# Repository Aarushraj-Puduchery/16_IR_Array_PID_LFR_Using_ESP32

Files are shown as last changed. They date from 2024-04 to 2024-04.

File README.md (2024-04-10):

# 16_IR_Array_PID_LFR_Using_ESP32

This is my Second Attempt to make a Line Follower Bot, I tried to correct the mistakes I made in my first LFR and here we go This is my new 16 IR Sensor Line Follower Bot using ESP32.

Why ESP32 because it has a High Clock Speed.

A line follower bot is a type of autonomous robotic vehicle designed to follow a predefined path or track marked with contrasting lines, typically black on a light-coloured surface or vice versa. These robots employ a combination of sensors, such as infrared or optical sensors, to detect the contrast between the line and the surrounding area. By continuously analyzing the sensor data, the bot makes real-time decisions on how to adjust its wheels or propulsion system to stay centred on the line.

Line follower bots are popular in robotics competitions and educational settings, as they provide an engaging way to introduce students and enthusiasts to basic robotics principles, sensor technology, and programming. They serve as a fundamental example of closed-loop control systems and can be customized with various features, like obstacle avoidance and speed adjustments, to make them more versatile and adaptable to different scenarios. Line follower bots can be a great starting point for those interested in exploring the world of robotics and automation.

A PID Line Follower Bot using an ESP32 Microcontroller is a small autonomous robot that uses infrared sensors to follow a designated path. It employs a PID (Proportional-Integral-Derivative) control algorithm to continuously adjust its motor speeds based on sensor feedback, maintaining alignment with the path. The ESP32 microcontroller processes the sensor data and sends control signals to the motors, allowing the bot to track lines, it is a popular choice for educational robotics projects and competitions.

## LFR Images

|Top View|Bottom View|
|---|---|
|Left view|Right View|

## Schematic Diagram

Schematic_New-16-ir-array-PID-LFR

## Chassis Design

|Components Placement|LFR Chassic|
|---|---|

## Wheels Design

|||
|---|---|
|||

>[!NOTE]
>Wheels Design Files are Uploaded and Can be 3D Printed Directly.

## Menu Graphic

|Start|Settings|Kp|
|---|---|---|
|Kd|Calibrate|Sensor Values|
|Run|

## Dry Run Video

https://github.com/Aarushraj-Puduchery/16_IR_Array_PID_LFR_Using_ESP32/assets/97360295/b0accbfe-f4fa-431e-92e3-81439fa5fb1b

## Components List
|S.No|  Name  | Cost | Quantity | Total Cost | Link |
|---| --- | --- | --- | --- | --- |
|1| ESP32 38 pin Development Board | ₹463.00 | 1 | ₹463.00 | https://robu.in/product/esp32-38pin-development-board-wifibluetooth-ultra-low-power-consumption-dual-core/ |
|2| TCRT5000 - Reflective Infrared Optical Sensor | ₹14.00 | 16 | ₹84.00 | https://www.electronicscomp.com/tcrt-5000-reflective-infrared-optical-sensor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 |
|3| CD74HC4067 16 Channel Multiplexer | ₹47.00 | 1 | ₹47.00 | https://www.electronicscomp.com/cd74hc4067-16-channel-multiplexer-breakout-board-module-india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 |
|4| N20-12V-1000 Rpm Micro Metal Gear Motor DC Encoder | ₹448.00 | 2 | ₹1792.00 | https://robokits.co.in/motors/n20-metal-gear-micro-motors/n20-metal-gear-encoder-motor/ga12-n20-12v-1000-rpm-all-metal-gear-micro-dc-encoder-motor-with-precious-meta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 |
|5| TB6612FNG Dual Channel Motor Driver | ₹349.00 | 1 | ₹349.00 | https://www.robojunkies.com/products/tb6612fng-dual-channel-motor-driver-breakout |
|6| Mounting Bracket for N20 Micro Gear motors | ₹29.00 | 2 | ₹58.00 | https://robu.in/product/mounting-bracket-n20-micro-gear-motors/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 |
|7| Mini MP1584 DC-DC 3A Adjustable Buck module | ₹48.00 | 1 | ₹48.00 | https://robu.in/product/mini-mp1584-dc-dc-adjustable-buck-module-3a/ |
|8| N20 mini-vacuum steel-ball caster wheel | ₹75.00 | 1 | ₹75.00 | https://robu.in/product/ball-castors/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 |
|9| Orange 850mah 3S 30C/60C (11.1V) Lithium Polymer Battery Pack | ₹999.00 | 1 | ₹999.00 | https://robu.in/product/orange-850mah-3s-30c-60c-lithium-polymer-battery-pack-lipo/ |
|10| Nylon XT60 Connectors Male/Female (1 pairs) | ₹69.00 | 1 | ₹69.00 | https://robu.in/product/amass-nylon-xt60-connectors-male-female-pair/ |
|11| Cricket Bat Grip | ₹100.00 | 1 | ₹100.00 | Local Shop |
|12| 1.3 inch 128×64 White OLED Display | ₹359.00 | 1 | ₹359.00 | https://robu.in/product/1-3-inch-i2c-iic-oled-lcd-module-4pin-with-vcc-gnd-white/ |
|13| 5 x 7 cm Universal PCB Prototype Board Single-Sided 2.54mm Hole Pitch | ₹33.00 | 2 | ₹66.00 | https://robu.in/product/5-x-7-cm-universal-pcb-prototype-board-single-sided-2-54mm-hole-pitch/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 | 
|14| 3 Pin SPDT Toggle switch | ₹70.00 | 1 | ₹70.00 | https://robu.in/product/5a-3-pin-spdt-toggle-switch/ |
|15| Tactile Push Button | ₹5.00 | 6 | ₹30.00 | https://robu.in/product/12x12x7-3mm-tactile-push-button-switch-round/ |
|16| Female Header pins | ₹20.00 | 5 | ₹100.00 | https://robu.in/product/2-54mm-1x40-pin-female-single-row-header-strip-pack-of-10/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 |
|17| Laser Cutting For Chassis | ₹205.00 | 1 | ₹205.00 | https://robu.in/product/online-laser-cutting-service/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 |
|18| 4mm SPDT 1P2T Slide Switch | ₹5.00 | 2 | ₹10.00 | https://robu.in/product/4mm-spdt-1p2t-slide-switch-pack-of-10/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 |
|19| 10k resistor 1/4W | ₹0.50 | 22 | ₹11.00 | https://robu.in/product/10k-ohm-0-25w-metal-film-resistor-pack-of-100/ |
|20| 220 resistor 1/4W | ₹0.50 | 16 | ₹8.00 | https://robu.in/product/220-ohm-resistor-0-25w-metal-film-pack-of-100/ |

> [!NOTE]
> Components price may vary.

## Source Code
1. `main.py` file which contains the basic setup and Run.
2. `bitmap.py` file contains all the menu graphics.
3. `KpValue.csv` and `KdValue.csv` are the files which store the kp and kd values.
4. `ssd1106.py` file is the library used for Oled display.
5. `framebuf.py` file is the library used for displaying graphics on Oled display.

>[!IMPORTANT]
>All the Files must be saved on the ESP32 Memory.

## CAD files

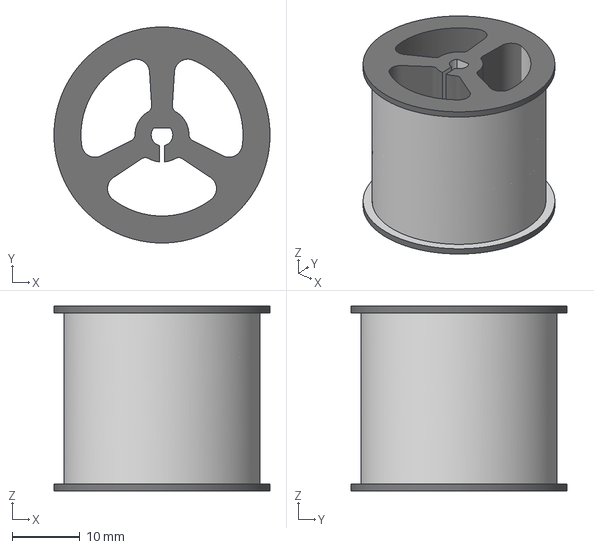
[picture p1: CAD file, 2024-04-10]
3D Printed Wheels Files/N20 Motor Wheel(2.7cm)_19 March v1.3mf
32.0 x 32.0 x 27.4 mm

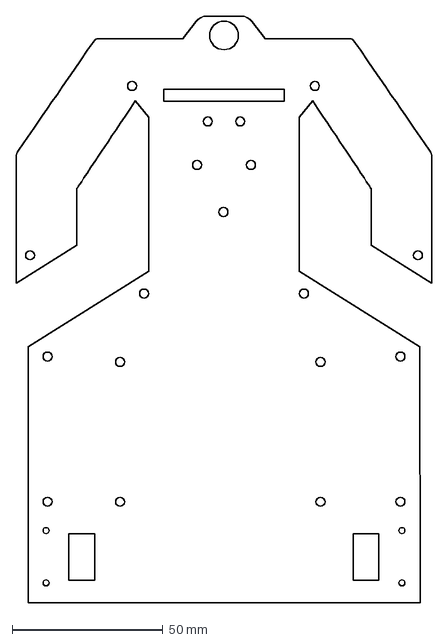
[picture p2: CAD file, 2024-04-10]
LFR Chassic Design/LFR Chassic.dxf
137.8 x 194.6 mm

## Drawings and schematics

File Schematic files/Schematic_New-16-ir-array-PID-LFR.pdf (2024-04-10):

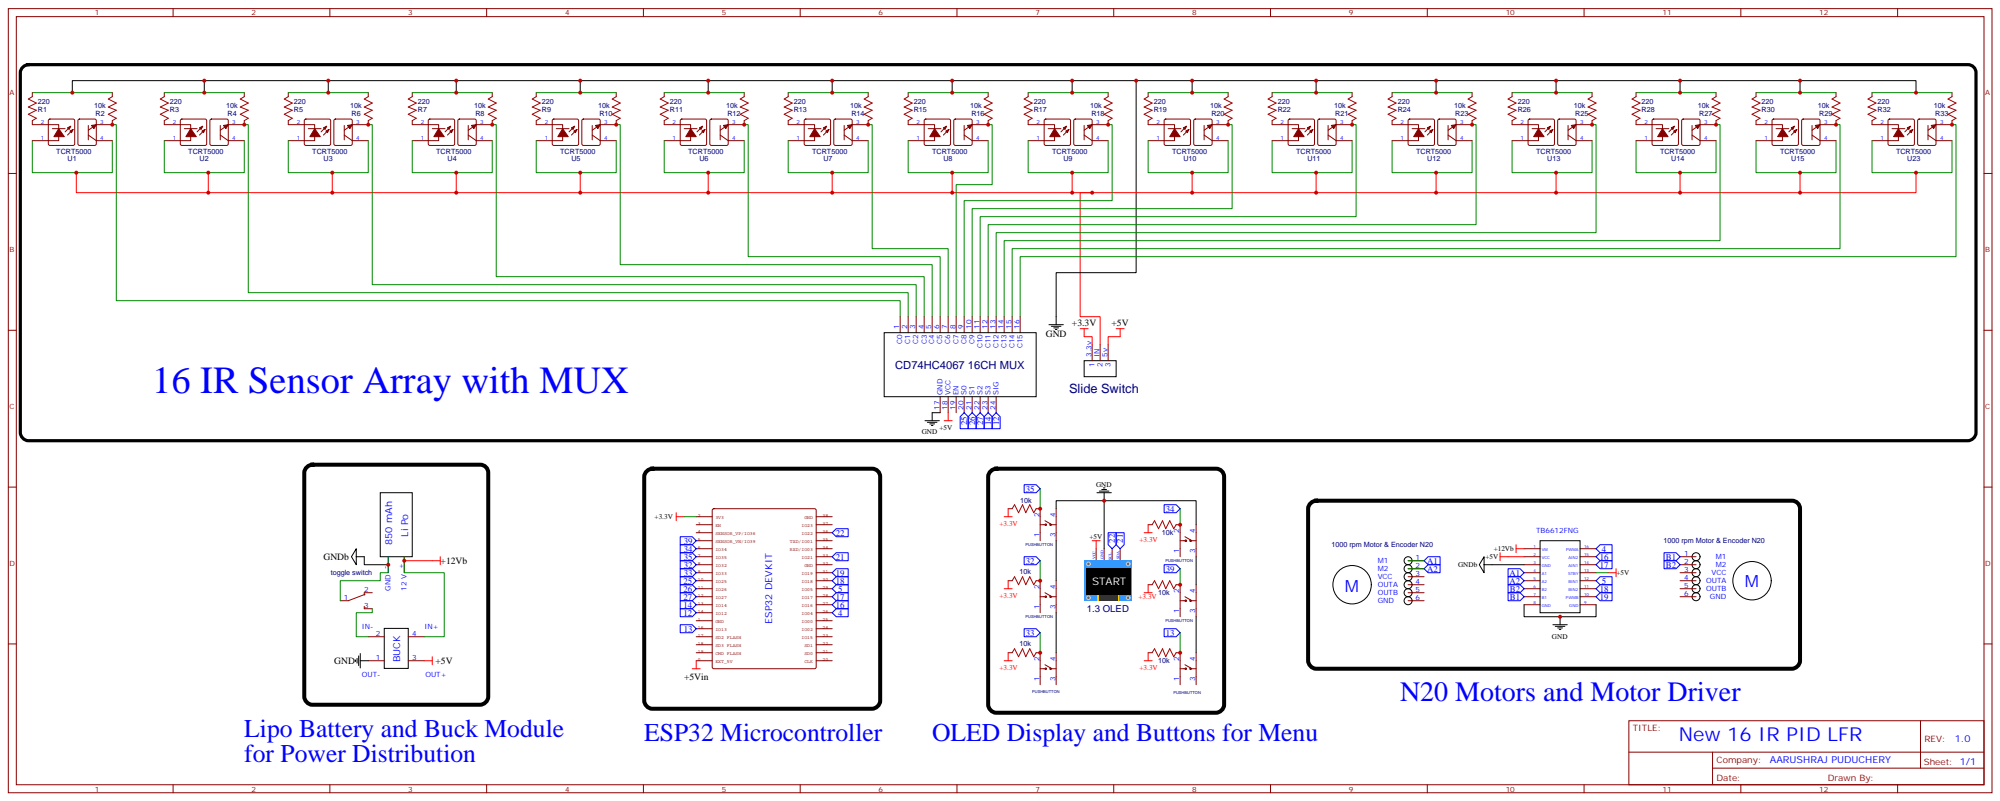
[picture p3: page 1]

16 IR Sensor Array with MUX

N20 Motors and Motor Driver

Lipo Battery and Buck Module
for Power Distribution

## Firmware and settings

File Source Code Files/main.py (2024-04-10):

#Simple Line Following Code using PID

from machine import Pin,PWM,I2C,ADC
from utime import sleep,sleep_ms,ticks_ms
import machine
import sh1106
import framebuf
import bitmap
machine.freq(240000000)

# Define pin numbers connected to buttons
UP = 35  # Up Button
DP = 34  # Down B
LP = 32  # Left B
RP = 39  # Right Button
SP = 33  # Select Button
BP = 13  # Back Button

UB = Pin(UP,Pin.IN)
DB = Pin(DP,Pin.IN)
LB = Pin(LP,Pin.IN)
RB = Pin(RP,Pin.IN)
SB = Pin(SP,Pin.IN)
BB = Pin(BP,Pin.IN)

count1,count2,count3 = 0,0,0
pr1 = 0
pr2,pr3 = 0,0
detime = 0
detime2 = 0
UBv,DBv,LBv,RBv,SBv,BBv = 0,0,0,0,0,0

def callback(pin):
    global count1,count2,count3,pr1,pr2,pr3,detime,detime2,UBv,DBv,LBv,RBv,SBv,BBv
    if str(pin) == "Pin(35)" and (ticks_ms() - detime > 300):
        count1 = count1 + 1
        UBv = 1
        print("UB")
        detime = ticks_ms()
    
    elif str(pin) == "Pin(34)" and (ticks_ms() - detime > 300):
        count1 = count1 - 1
        DBv = 1
        print("DB")
        detime = ticks_ms()

    elif str(pin) == "Pin(32)" and (ticks_ms() - detime > 300):
        count2 = count2 + 1
        LBv = 1
        print("LB")
        detime = ticks_ms()
        
    elif str(pin) == "Pin(39)" and (ticks_ms() - detime > 300):
        count2 = count2 - 1
        RBv = 1
        print("RB")
        detime = ticks_ms()
        
    elif str(pin) == "Pin(33)" and (ticks_ms() - detime2 > 300):
        count3 = count3 + 1
        SBv = 1
        print("SB")
        detime2 = ticks_ms()
        
    elif str(pin) == "Pin(13)" and (ticks_ms() - detime > 300):
        count3 = count3 - 1
        BBv = 1
        print("BB")
        detime = ticks_ms()


UB.irq(trigger=Pin.IRQ_FALLING, handler=callback)
DB.irq(trigger=Pin.IRQ_FALLING, handler=callback)
LB.irq(trigger=Pin.IRQ_FALLING, handler=callback)
RB.irq(trigger=Pin.IRQ_FALLING, handler=callback)
SB.irq(trigger=Pin.IRQ_FALLING, handler=callback)
BB.irq(trigger=Pin.IRQ_FALLING, handler=callback)

#Oled Display
sda=Pin(21)
scl=Pin(22)
i2c = I2C(0, scl=scl, sda=sda, freq=400000)
oled = sh1106.SH1106_I2C(128, 64, i2c, Pin(4), 0x3c)
oled.sleep(False)



#Motors
MAF = Pin(17,Pin.OUT)
MAR = Pin(16,Pin.OUT)
MBF = Pin(5,Pin.OUT)
MBR = Pin(18,Pin.OUT)
MAC = PWM(Pin(4))
MBC = PWM(Pin(19))

MAC.freq(1000)
MBC.freq(1000)

# Define pins for multiplexer control
sensor_value = [0,0,0,0,0,0,0,0,0,0,0,0,0,0,0,0]
s0 = Pin(25, Pin.OUT)
s1 = Pin(26, Pin.OUT)
s2 = Pin(27, Pin.OUT)
s3 = Pin(14, Pin.OUT)

# Define analog input pin
analog_pin = Pin(12)


maxvalue = [0,0,0,0,0,0,0,0,0,0,0,0,0,0,0,0]
minvalue = [0,0,0,0,0,0,0,0,0,0,0,0,0,0,0,0]
threshold = [0,0,0,0,0,0,0,0,0,0,0,0,0,0,0,0]
sensor_val = [0,0,0,0,0,0,0,0,0,0,0,0,0,0,0,0]
sensor_arr = [0,0,0,0,0,0,0,0,0,0,0,0,0,0,0,0]
ir_val = [0,0,0,0,0,0,0,0,0,0,0,0,0,0,0,0]
mode = -1

isBlackLine = 1
P, D, I, PIDvalue = 0,0,0,0
PreviousError = 0
error = 0.0
sensorWeight = [ 9, 7, 5, 4, 3, 2, 1, 0, 0, -1, -2, -3, -4, -5, -7, -9 ]
lfSpeed = 36000
currentSpeed = 35000
activeSensors = 0
op = 0

KpFile = open("kpfile.csv","r")
Kp = float(KpFile.read())
KdFile = open("kdfile.csv","r")
Kd = float(KdFile.read())
KpFile.close()
KdFile.close()
Ki = 0

def read_ir_sensor(channel):
    s0.value(channel & 0x01)
    s1.value((channel >> 1) & 0x01)
    s2.value((channel >> 2) & 0x01)
    s3.value((channel >> 3) & 0x01)
    sleep_ms(1)  # Wait for the channel to settle
    adc = ADC(analog_pin)
    adc.atten(ADC.ATTN_11DB)
    return adc.read()

def motor1run(motorSpeed):
    if (motorSpeed > 0):
        MAF.value(1)
        MAR.value(0)
        MAC.duty_u16(int(motorSpeed))
    elif(motorSpeed < 0):
        MAF.value(0)
        MAR.value(1)
        MAC.duty_u16(abs(int(motorSpeed)))
    else:
        MAF.value(1)
        MAR.value(1)
        MAC.duty_u16(0)

def motor2run(motorSpeed):
    if (motorSpeed > 0):
        MBF.value(1)
        MBR.value(0)
        MBC.duty_u16(int(motorSpeed))
    elif(motorSpeed < 0):
        MBF.value(0)
        MBR.value(1)
        MBC.duty_u16(abs(int(motorSpeed)))
    else:
        MBF.value(1)
        MBR.value(1)
        MBC.duty_u16(0)

def calibrate():
    motor1run(0)
    motor2run(0)
    fbuf = framebuf.FrameBuffer(bitmap.calibrate_text, 128, 64, framebuf.MONO_HLSB)
    oled.fill(0)
    oled.blit(fbuf, 0, 0, 0)          
    oled.show()
    #step 1: fill the min and max list with current values
    for i in range(16):
        minvalue[i] = read_ir_sensor(i)
        maxvalue[i] = read_ir_sensor(i)

    #step 2: sort the max and min values of all sensors by moving the bot left and right
    for j in range(80):
        motor1run(27000)
        motor2run(-27000)
        for i in range(16):
            if(read_ir_sensor(i) < minvalue[i]):
                minvalue[i] = read_ir_sensor(i)
            if(read_ir_sensor(i) > maxvalue[i]):
                maxvalue[i] = read_ir_sensor(i)

    #step 3: calculate the threshold values
    print("threshold")
    for i in range(16):
        threshold[i] = (minvalue[i] + maxvalue[i])/2
        print(threshold[i],end=" ")
    motor1run(0)
    motor2run(0)

def convert(x, in_min, in_max, out_min, out_max):
    return (x - in_min) * (out_max - out_min) // (in_max - in_min) + out_min
    
def readline():
    global onLine,isBlackLine,minvalue,maxvalue
    onLine = 0
    for i in range(16):
        if(isBlackLine):
            sensor_val[i] = convert(read_ir_sensor(i), minvalue[i], maxvalue[i], 0, 1000)
        else:
            sensor_val[i] = convert(read_ir_sensor(i), minvalue[i], maxvalue[i], 1000, 0)
        
        sensor_val[i] = min(max(sensor_val[i], 0), 1000)
        sensor_arr[i] = sensor_val[i] < 450
        if(sensor_arr[i]):
            onLine = 1
            
        if(isBlackLine == 1 and sensor_arr[i]):
            onLine = 1
        if(isBlackLine == 0 and not(sensor_arr[i])):
            onLine = 1

def linefollow():
    global error,activeSensors,P,I,D,PIDvalue,PreviousError,lsp,Kp,Ki,Kd,rsp
    error=0
    activeSensors = 0
    for i in range(16):
        error = error + (sensorWeight[i] * sensor_arr[i] * (1000 - sensor_val[i]))
        activeSensors += sensor_arr[i]
    
    error = error/activeSensors
    
    P = error
    I = I + error
    D = error - PreviousError
    
    PIDvalue = (Kp * P) + (Ki * I) + (Kd * D)
    PreviousError = error
    
    lsp = currentSpeed - PIDvalue
    rsp = currentSpeed + PIDvalue
    
    fbuf = framebuf.FrameBuffer(bitmap.letgo_text, 128, 64, framebuf.MONO_HLSB)
    oled.fill(0)
    oled.blit(fbuf, 0, 0, 0)
    oled.text("lsp = ",0,40)
    oled.text("rsp = ",0,50)
    oled.text(str(lsp),45,40)
    oled.text(str(rsp),45,50)
    oled.show()
    
    if(lsp > 65535):
        lsp = 65535
    if(lsp < 0):
        lsp = 0
    if(rsp > 65535):
        rsp = 65535
    if(rsp < 0):
        rsp = 0
    motor1run(lsp);
    motor2run(rsp);
    
def ir_show():
    global ir_val
    for i in range(1,17):
        if (i <= 8):
            oled.text(str(i),((8*(i-1))-1),55)
        else:
            oled.text(str(17 - i),(8*(i-1)-1),55)
        oled.show()
    while True:
        oled.fill_rect(0,0,128,45,0)
        for i in range(16):
            ir_val[i] = convert(read_ir_sensor(i), minvalue[i], maxvalue[i], 1, 45)
            ir_val[i] = min(max(ir_val[i],1),45)
        for i in range(16):
            oled.fill_rect((i)*8,0,6,45,1)
            oled.fill_rect((i)*8,0,6,45 - ir_val[i],0)
        oled.show()
        if SBv == 1:
            break

    
def setup_val():
    global count1,count2,count3,Kp,Kd,UBv,DBv,LBv,RBv,SBv,BBv,mode,op
    menu = [bitmap.start_menu, bitmap.setting_menu]
    fbuf = framebuf.FrameBuffer(menu[count1], 128, 64, framebuf.MONO_HLSB)
    oled.blit(fbuf, 0, 0, 0)          
    oled.show()
    oled.fill(0)
    if BBv == 1:
        fbuf = framebuf.FrameBuffer(menu[count1], 128, 64, framebuf.MONO_HLSB)
        oled.blit(fbuf, 0, 0, 0)    
        oled.show()
        BBv = 0
        
    if (UBv == 1) or (DBv == 1):
        count1 = (count1) % len(menu)
        oled.fill(0)
        fbuf = framebuf.FrameBuffer(menu[count1], 128, 64, framebuf.MONO_HLSB)
        oled.blit(fbuf, 0, 0, 0)
        oled.show()
        UBv, DBv = 0,0
    if count1 == 0 and SBv == 1:
        mode = 1
    if count1 == 1 and SBv == 1:
        count1 = 0
        SBv = 0
        oled.fill(0)
        oled.show()
        while True:
            setting = [bitmap.Kp_menu,bitmap.Kd_menu]
            settingfile = ["kp","kd"]
            fbuf = framebuf.FrameBuffer(setting[count1], 128, 64, framebuf.MONO_HLSB)
            oled.fill(0)
            oled.blit(fbuf, 0, 0, 0)          
            oled.show()
            if (UBv == 1) or (DBv == 1):
                count1 = (count1) % len(setting)
                fbuf = framebuf.FrameBuffer(setting[count1], 128, 64, framebuf.MONO_HLSB)
                oled.fill(0)
                oled.blit(fbuf, 0, 0, 0)          
                oled.show()
                UBv, DBv = 0,0
                op = count1
            
            if SBv == 1:
                count1 = 0
                oled.fill(0)
                BBv = 0
                while True:
                    SBv = 0
                    if UBv == 1 or DBv == 1:
                        count1 = max(-3,min(count1,4))
                        UBv, DBv = 0,0
                        oled.fill(0)
                    oled.text(str(10**(-1*count1)),55,40)
                    oled.show()
                    KpFile = open(settingfile[op]+"file.csv","r")
                    Kp = float(KpFile.read())
                    KpText = str(Kp)
                    oled.text(KpText, 35, 18)
                    oled.show()
                    KpFile.close()
                    if LBv == 1:
                        Kp = (Kp - (1*pow(10,-1*count1)))
                        KpFile = open(settingfile[op]+"file.csv","r+")
                        KpFile.seek(0)
                        KpText = str(Kp)
                        KpFile.write(KpText)
                        KpFile.close()
                        oled.text(KpText, 35, 18)
                        oled.show()
                        oled.fill(0)
                        LBv = 0
                    if RBv == 1:
                        Kp = (Kp + (1*pow(10,-1*count1)))
                        KpFile = open(settingfile[op]+"file.csv","r+")
                        KpFile.seek(0)
                        KpText = str(Kp)
                        KpFile.write(KpText)
                        KpFile.close()
                        oled.text(KpText, 35, 18)
                        oled.show()
                        oled.fill(0)
                        RBv = 0
                    if BBv == 1:
                        oled.fill(0)
                        oled.text(settingfile[count1], 0, 0)
                        oled.show()
                        BBv = 0
                        break      
            if BBv == 1:
                BBv = 0
                break
       

while True:
    setup_val()
    if mode == 1:
        mode = 0
        break

oled.fill(0)
KpFile = open("kpfile.csv","r")
KpT = float(KpFile.read())
KpText = str(KpT)
KdFile = open("kdfile.csv","r")
KdT = float(KdFile.read())
KdText = str(KdT)
oled.text("Kp", 50, 0)
oled.text((KpText), 22, 20)
oled.text("Kd", 50, 35)
oled.text((KdText), 22, 55)
oled.show()
KpFile.close()
KdFile.close()
SBv = 0
while SBv == 0:
    pass
calibrate()
SBv = 0
BBv = 0
while SBv == 0:
    ir_show()
    motor1run(0)
    motor2run(0)

SBv = 0
fbuf = framebuf.FrameBuffer(bitmap.letgo_text, 128, 64, framebuf.MONO_HLSB)
oled.fill(0)
oled.blit(fbuf, 0, 0, 0)          
oled.show()
while True:
    readline()
#     if (currentSpeed < lfSpeed):
#         currentSpeed = currentSpeed + 4
    if (onLine == 1):
        linefollow()
    else:
        if error > 0:
            motor1run(-40000)
            motor2run(lsp)
        else:
            motor1run(rsp)
            motor2run(-40000)

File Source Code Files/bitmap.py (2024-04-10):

start_menu = bytearray(b"\x00\x00\x00\x00\x00\x00\x00\x00\x00\x00\x00\x00\x00\x00\x00\x00\x00\x00\x00\x00\x00\x00\x60\x00\x00\x03\x00\x00\x00\x00\x00\x00\x00\x00\x00\x00\x00\x00\xe0\x00\x00\x03\x80\x00\x00\x00\x00\x00\x00\x00\x00\x00\x00\x01\x30\x00\x00\x06\x40\x00\x00\x00\x00\x00\x00\x00\x00\x00\x00\x02\x30\x00\x00\x06\x30\x00\x00\x00\x00\x00\x00\x00\x00\x00\x00\x0c\x18\x00\x00\x0e\x18\x00\x00\x00\x00\x00\x00\x00\x00\x00\x00\x3c\x18\x00\x00\x0c\x1e\x00\x00\x00\x00\x00\x00\x00\x00\x00\x01\xfc\x3c\x00\x00\x1e\x1f\xc0\x00\x00\x00\x00\x00\x00\x00\x00\x1e\x7e\xfe\x00\x00\x1f\xbf\x3c\x00\x00\x00\x00\x00\x00\x00\x00\xf0\x3e\xfe\x00\x00\x3f\xde\x03\x80\x00\x00\x00\x00\x00\x00\x07\xf0\x38\xfe\x00\x00\x3f\x8e\x03\xe0\x00\x00\x00\x00\x00\x00\x39\xf0\x00\x73\x00\x00\x67\x80\x07\xce\x00\x00\x00\x00\x00\x00\x20\xf0\x60\x63\x00\x00\x61\x03\x07\xc2\x00\x00\x00\x00\x00\x01\xc0\xf3\xf0\x01\x80\x00\xe0\x03\xe7\x81\x80\x00\x00\x00\x00\x03\xc0\x83\xf0\xc1\x80\x00\xc1\xc7\xe0\x81\xe0\x00\x00\x00\x00\x07\xe1\x83\xf3\xc3\xc0\x01\xe1\xf7\xe0\xc3\xf0\x00\x00\x00\x00\x07\xf7\x81\xe3\xe7\xc0\x01\xf3\xf3\xc0\xf3\xf0\x00\x00\x00\x00\x03\xff\xc0\x03\xff\xe0\x03\xff\xf0\x00\xf9\xe0\x00\x00\x00\x00\x03\x8f\xc6\x03\xcf\xe0\x03\xf9\xe0\x38\xf8\xe0\x00\x00\x00\x00\x01\x87\x9f\x01\x8e\x30\x07\x38\x40\x7c\xf0\x40\x00\x00\x00\x00\x01\x86\x1f\x80\x04\x38\x06\x10\x00\xfc\x20\x40\x00\x00\x00\x00\x00\x84\x0c\x0f\x04\x18\x0e\x10\x38\x18\x00\xc0\x00\x00\x00\x00\x00\xcc\x00\x3f\x0c\x38\x0e\x18\x7e\x00\x1c\x00\x00\x00\x00\x00\x00\x5c\x00\x1f\x1c\x7c\x0c\x1e\x7c\x04\x1e\x00\x00\x00\x00\x00\x00\x7e\x78\x1c\x3f\x8c\x18\xfe\x0c\x0f\x9f\x00\x00\x00\x00\x00\x00\x3e\xfc\x10\x3f\x86\x30\x7e\x00\x0f\xdf\x00\x00\x00\x00\x00\x00\x38\xf8\xf0\x3e\x06\x30\x1e\x07\xcf\x86\x00\x00\x00\x00\x00\x00\x10\x71\xf1\xf8\x06\x70\x07\xc7\xe7\x80\x00\x00\x00\x00\x00\x00\x00\x01\xff\x80\x02\x60\x00\x7f\xc0\x00\x00\x00\x00\x00\x00\x00\x00\x01\xf8\x00\x00\x60\x00\x0f\xc0\x00\x00\x00\x00\x00\x00\x00\x01\xc7\x80\x00\x00\xc0\x00\x00\x71\xc8\x00\x00\x00\x00\x00\x00\x0f\xec\x00\x00\x00\xc0\x00\x00\x19\xf8\x00\x00\x00\x00\x00\x00\x07\xf0\x00\x00\x01\x80\x00\x00\x07\xf0\x00\x00\x00\x00\x00\x00\x07\xc0\x00\x00\x01\x80\x00\x00\x01\xe0\x00\x00\x00\x00\x00\x00\x03\x80\x00\x00\x03\x20\x00\x00\x00\xe0\x00\x00\x00\x00\x00\x00\x03\x00\x00\x00\x03\x70\x00\x00\x00\x60\x00\x00\x00\x00\x00\x00\x00\x00\x00\x00\x06\x70\x00\x00\x00\x00\x00\x00\x00\x00\x00\x00\x00\x00\x00\x00\x06\x30\x00\x00\x00\x00\x00\x00\x00\x00\x00\x00\x00\x00\x00\x00\x00\x00\x00\x00\x00\x00\x00\x00\x00\x00\x00\x00\x00\x00\x00\x00\x00\x00\x00\x00\x00\x00\x00\x00\x00\x00\x00\x00\x00\x00\x00\x00\x00\x00\x00\x00\x00\x00\x00\x00\x00\x00\x00\x00\x3d\xc0\x00\x0c\x00\x00\x00\x00\x00\x01\x00\x00\x00\x00\x00\x00\x60\x30\xef\xf4\x03\x80\x08\xe0\x3d\xfc\x80\x00\x00\x00\x00\x00\x83\xa1\x80\x00\x0c\x40\x10\x00\x20\x00\x80\x00\x00\x00\x00\x01\x08\x63\x00\x02\x18\x40\x10\x08\x60\x00\x80\x00\x00\x00\x00\x01\x0f\xc3\xfe\x7e\x18\x20\x31\x88\xbf\x8f\x80\x00\x00\x00\x00\x03\x04\x03\x86\x00\x29\x20\x32\x88\xe1\xc8\x00\x00\x00\x00\x00\x03\x82\x03\x0a\x3c\x49\x90\x31\x88\xc2\x8f\x00\x00\x00\x00\x00\x00\x81\x80\xfa\x00\x43\x90\x33\x10\x1e\x80\x00\x00\x00\x00\x00\x01\x70\x40\x0a\x20\x53\xc8\x30\x20\x00\x80\x00\x00\x00\x00\x00\x00\xcc\x30\x0a\x20\x51\xc8\x30\x20\x01\x40\x00\x00\x00\x00\x00\x00\x3b\x08\x02\x20\x50\x04\x12\x10\x01\x44\x00\x00\x00\x00\x00\x00\x04\x88\x04\x20\xa1\xe4\x13\x08\x01\x44\x00\x00\x00\x00\x00\x00\x02\x44\x05\x00\xa1\x62\x12\x88\x01\x44\x00\x00\x00\x00\x00\x00\x41\x44\x05\x10\xa1\x62\x13\x44\x01\x44\x00\x00\x00\x00\x00\x00\xc1\xc8\x05\x10\xc3\xf3\x12\xc2\x01\x44\x00\x00\x00\x00\x00\x01\x01\x98\x05\x10\xc1\x31\x32\x62\x01\x44\x00\x00\x00\x00\x00\x01\xce\x10\x05\x11\x43\x3f\xb2\x41\x01\x44\x00\x00\x00\x00\x00\x00\x70\x60\x05\xe1\xe6\x37\xbe\x2f\x01\x7c\x00\x00\x00\x00\x00\x00\x4f\x80\x06\x61\x84\x1c\x34\x1a\x01\xc8\x00\x00\x00\x00\x00\x00\x3f\x00\x07\x81\xf8\x00\x30\x00\x01\xf0\x00\x00\x00\x00\x00\x00\x00\x00\x00\x01\xc0\x00\x00\x00\x00\x00\x00\x00\x00\x00\x00\x00\x00\x00\x00\x00\x00\x00\x00\x00\x00\x00\x00\x00\x00\x00\x00\x00\x00\x00\x00\x00\x00\x00\x00\x00\x00\x00\x00\x00\x00")
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
